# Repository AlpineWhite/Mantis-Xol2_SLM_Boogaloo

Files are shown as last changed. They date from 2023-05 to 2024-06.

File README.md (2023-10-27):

# SLMantis Xol 2 Aluminum Boogaloo (Slimfast)
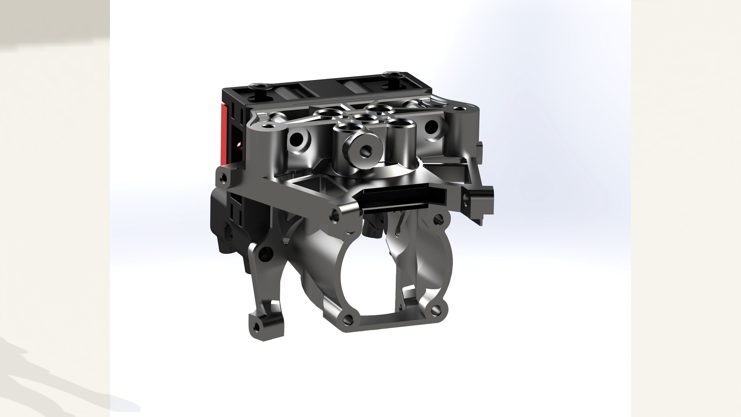
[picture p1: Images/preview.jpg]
Carriage Assembly The Metal Bits
   

## Description
Originally a project to slap 5020 blower fans onto Mantis, this toolhead variant started as an attempt to improve parts cooling, spurred on by Derpimus' noted cooling woes on his DOOMCube. After finding that the 5020s were just plain too fat to fit without looking like a standard Ender 3 Thingiverse special, I abandoned the large fan dream in favor of better cooling efficiency and lighter weight. This new and improved dream was also corrupted by my then budding and now all-consuming love for worm gears.

This was further pushed into the territory of abomination By deadwood83 who decided that plastic just wasn't metal enough, but a straight metal print was too heavy.  Since he was too plebian to have a worm-geared extruder, only Sherpa Mini support currently exists.

https://discord.gg/armchairengineeringsux

### Quick Links:
[Assembly / Tapping](https://github.com/AlpineWhite/Mantis-Xol2_SLM_Boogaloo/blob/main/Assembly.md)<br/>
[DragNet Bending Jig Usage](https://github.com/AlpineWhite/Mantis-Xol2_SLM_Boogaloo/tree/main/STL/Nets/DragNet/Bending%20Jig)<br/>
[RapidNet Bending Jig Usage](https://github.com/AlpineWhite/Mantis-Xol2_SLM_Boogaloo/tree/main/STL/Nets/RapidNet)<br/>
[RapidNet Grinding Jig Usage](https://github.com/AlpineWhite/Mantis-Xol2_SLM_Boogaloo/tree/main/STL/Nets/RapidNet/Grinding%20Jig) (For the Rapido Hotend)<br/>
[Probemounts](https://github.com/AlpineWhite/Mantis-Xol2_SLM_Boogaloo/tree/main/STL/XOL2%20SLiM%20V1.1%20%2B%20Probes/Probemounts)<br/>
[Breakout Toolhead PCB](https://github.com/AlpineWhite/Mantis-Xol2_SLM_Boogaloo/tree/main/SLiM%20PCB) <br/>
[My CNC Goals / How to Support Development](https://www.buymeacoffee.com/deadwood/first-post-first-steps)

## New Features for SLiMantis Xol 2
 - Cooler: Think Xol is ugly? This is not any better. But the entire hotend is now a heatsink.
 - Metaler: There is so much more metal. All inserts are replaced by tapped holes.
 - Rigid-er-er: Look at all that metal in the all-metal construction.
 - Supports Rapido, Dragon, Dragon UHF, Dragon+T-Volcano, Red Lizard all on one hotend mount.
 - Nets are created to attach the bottom of each hotend (except lizard) to the carriage. Nets are 304 stainless with 3d printed bending jigs. 

#### Features:
 - Better airflow than Stealthburner (6-7 CFM through short ducts vs 4.6-5.2 CFM through long ducts)
 - No inserts. No worries about thermal deformation.
 - Support for Sherpa Mini-pattern extruder mounting.
 - Symmetrical ziptie options.
 - Printed holes are already tap size.
 - Support for Whoppingpochard's Klicky PCB, OG Klicky, and bacon; but hardpoints on the bottom of the carriage allow for a modular approach to probing.
 - Top hardpoints allow development of custom tophats for your toolhead. Umbilical? Sure. Mantis tophat to bolt more stuff to your toolhead? Sure. Extruder apater plates which tie the carriage and hotend mount together? Sure.
 - Cross-compatibility with most of the XOL2 printed parts. You can combine metal hotend mount with a printed carriage, vice-versa, use printed ducts, printed faceplates, LED holder, nozzle camera mounts, etc. 
 - X axis microswitch in either direction (min/max/both except Kevin hates you for wanting to know your actual axis limits).
 
#### Future Development (No ETA):
 - MGN12 Carriage
 - Unnamed things because we have not discovered what else we may want to paste onto this.
 - Fancy ikon rail carriage support 

## Build Notes:
This toolhead might require other modifications to retain full functionality of your printer. 
 - All test machines used for this mod had Rama's front idlers which have a much lower profile compared to stock Voron front idlers. The fan assemblies might conflict and reduce usable X travel.
 - The Klicky Probe carriage that was adapted was originally designed for the Dragon hotend. You'll need to use a taller probe body to reach the bed such as the one used by [Unklicky BFP](https://github.com/majarspeed/Unklicky). *This isn't an issue for Euclid or PCB Klicky*.
## Bill of Materials 
|Item|Count|Note|
|----|-|--|
|Rapido|1|
|Sherpa Mini|1|CNC optional, but rigider-er-er|
|M2 Tap|1|[Use the tapered taps](https://www.amazon.com/gp/product/B07WGS6T3N) and WD-40 as lube|
|M2.5 Tap|1|
|M3 Tap|1|
|4010 24v blower fans|2|Add Polulu 3796 if you want the fancy 12v Deltas|
|2510 24v axial fan|1|
|M2x8 SHCS|6|
|M2x4 FHCS|2| Only for DragNet|
|M1.6 Low-Profile Nuts|2|Only for DragNet with T-Volcano|
|M2x12 SHCS|9|4 For Probe Mounts, 4 for fans, 1 for endstop|
|M2x6 SHCS|2|For Belt Pre-tension (optional)|
|M2.5x20 SHCS|4|For Cooling Fan|
|M2.5x8 90Deg FHCS|4|For Rapido mount|
|M3x8 BHCS|2|For Mount<->Carriage Lower Fasteners|
|M3x6 BHCS|1|For Sherpa K-mount|
|M3x10 90Deg FHCS|4|For carriage to rail mounting|
|M3x20-22 FHCS|4|Sherpa<->Hotend Mount and Hotend<->Carriage upper mount|
|D2F-5L Microswitch|1-2|
|M3x20-22 90Deg FHCS|2| For Hotend upper mounts on V1.1. 22mm gives 5mm of thread engagement. 20mm will work for both designs, just 22mm is slightly better for V1.1|
|ZIP TIES||

## Acknowledgement
[Long/Mandryd](https://github.com/mandryd/VoronUsers/tree/master/printer_mods/Long/Mantis_Dual_5015) for the Mantis toolhead.<br/>
[TheWarolf](https://github.com/TheWarolf/Voron-Personal-Mods/tree/main/V2/Long_Mantis_Toolhead) for the ERCF sensorized Hotend Mount.<br/>
[Derpimus](https://github.com/lraithel15133) for the exegesis, some CAD work, feedback, and just being a rad dude.<br/>
[KayosMaker](https://github.com/KayosMaker) for the MGN12 Klicky X-Carriage and CAN board mounts and spacers.<br/>
[JosAr](https://github.com/jlas1/Klicky-Probe) for Klicky.<br/>
[WhoppingPochard](https://github.com/tanaes) and [VinnyCordeiro](https://github.com/VinnyCordeiro/) for PCB Klicky.<br/>
[Nionio6915](https://github.com/nionio6915/Euclid_Probe) for Euclid. <br/>
[VoronDesign](https://github.com/VoronDesign) for this particular CoreXY flavor.<br/>
[AnnexEngineering](https://github.com/Annex-Engineering) for the Sherpa Mini and Double Folded Ascender extruders, and the K3 that influenced the air management of the ducts. And also for giving access to an early revision of the new DFA so it could be adapted for this toolhead.<br/>
[Clee](https://github.com/clee), you know what you did.  
[Takuya](https://github.com/T4KUUY4)... just added the 36mm SB2040 mount

Like my work? Want to support the cause?  I created a donation link because somebody asked how they can donate to me. [Here it is.](https://bmc.link/deadwood)

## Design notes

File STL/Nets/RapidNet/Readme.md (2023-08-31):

# RapidNet Bending Jig Usage
Print all parts at 100% infill.
All parts are in 'real' dimensions. You may need to scale 1% for shrinkage.
| Instruction | |
| --- | --- |
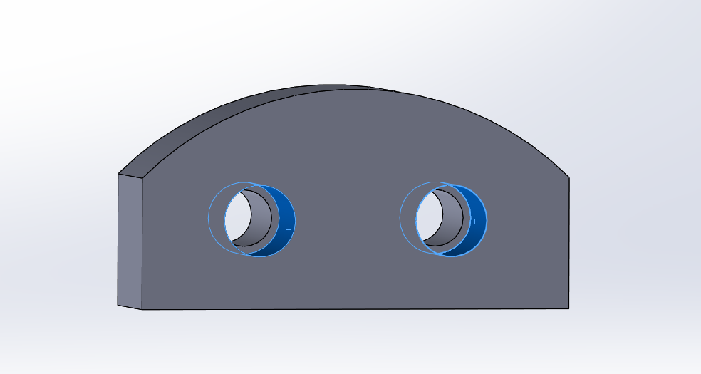
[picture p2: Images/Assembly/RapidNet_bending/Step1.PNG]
Clamp Heatsert Heatsert Installation
| Insert teo M3 heatserts into the clamping piece. This will interface with two M3x12SHCS.  |   |
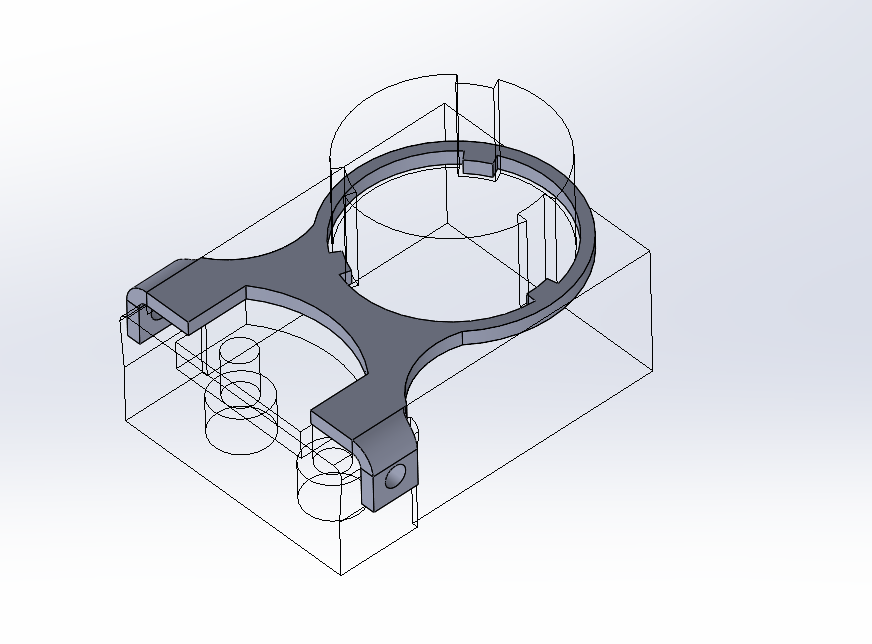
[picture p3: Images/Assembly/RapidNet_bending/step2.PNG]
Flat Positioning
| Lay the RapidNet flat into the bottom jig piece.  |    |
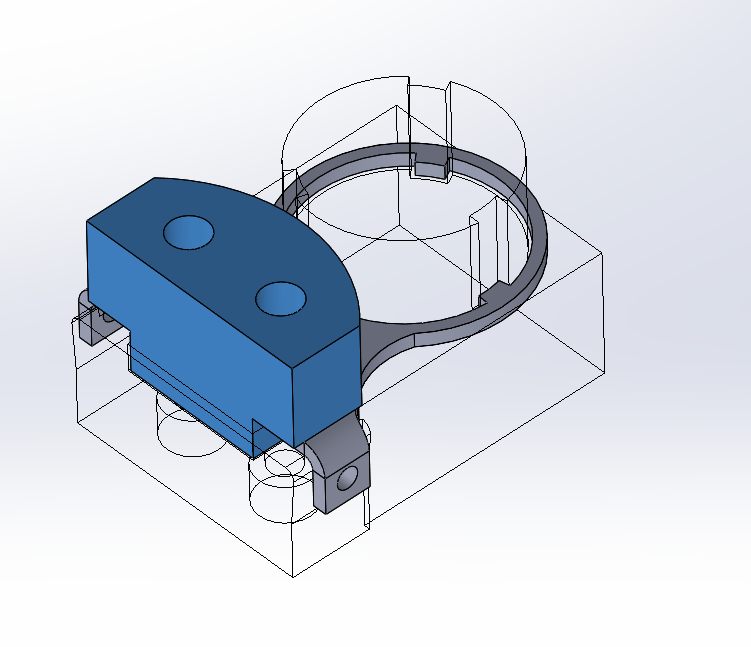
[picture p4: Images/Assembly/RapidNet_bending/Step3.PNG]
Clamping
| Insert the clamping piece into the recess, and fasten from the back with two M3 SHCS. |    |
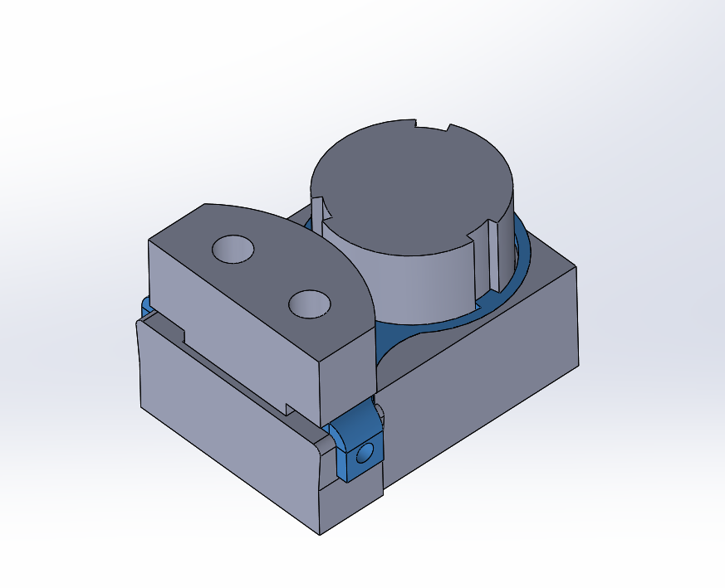
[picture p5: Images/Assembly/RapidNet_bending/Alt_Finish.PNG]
Hammertime Viseless Bending
| RECOMMENDED If you wish to use a hammer or other non-press/vise tool, press the tabs down against the plastic.  |   |
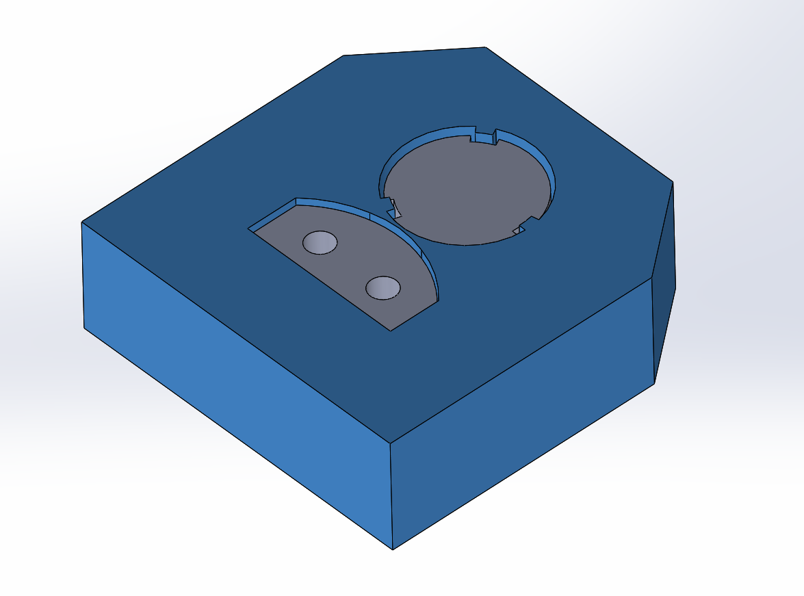
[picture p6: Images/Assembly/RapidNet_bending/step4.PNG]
Bending
| If using a vise or press, lay the top piece on the flat, and compress the sandwich to create the bend. |   |
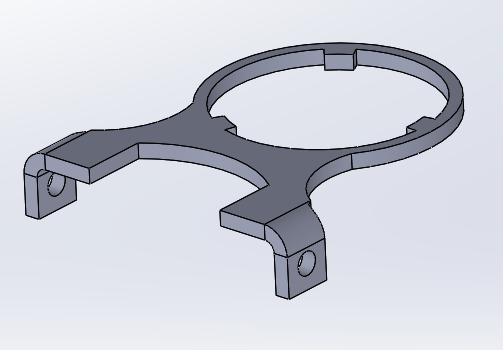
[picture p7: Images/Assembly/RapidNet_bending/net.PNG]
Finished Job Done
| Carefully remove the new-bent RapidNet from the jig. You may need to squeeze the tabs a little to compensate for springback. |   |

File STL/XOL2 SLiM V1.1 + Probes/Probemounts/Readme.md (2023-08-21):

For beacon:
 - There is a single part, but it must be mirrored to make each half of the mount. 
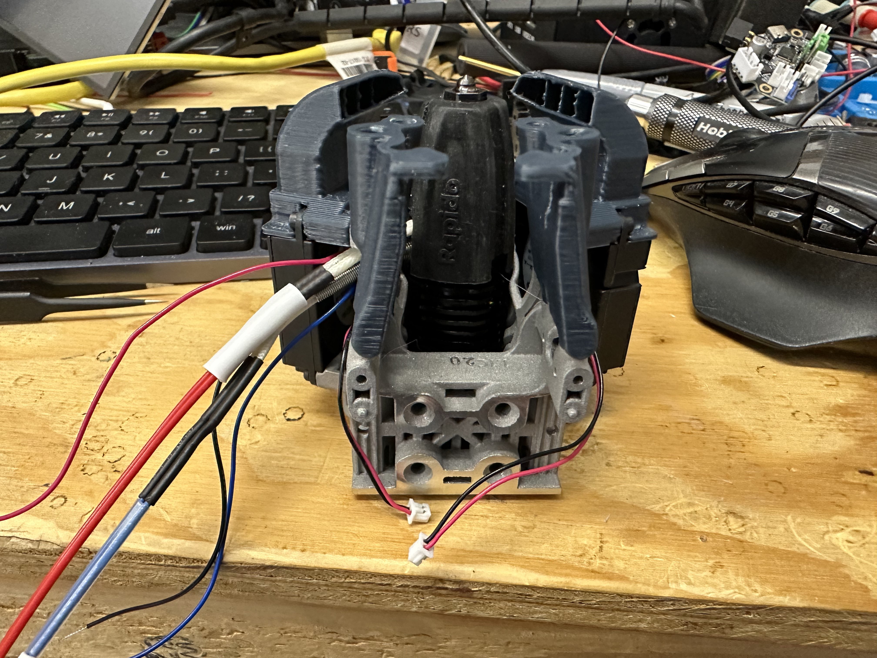
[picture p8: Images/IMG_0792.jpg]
Beacon Assembly Baconator


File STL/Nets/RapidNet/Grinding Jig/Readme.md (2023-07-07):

# RapidNet Grinding Jig Usage

| Instruction | |
| --- | --- |
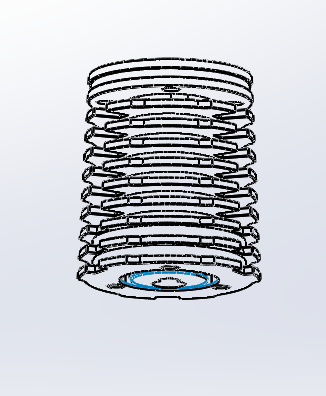
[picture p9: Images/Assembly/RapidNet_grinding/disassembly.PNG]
Disassemble Disassembly
| Remove the heater block from the Rapido and set aside. Keep the fasteners with the heater block. Only the heatsink is needed  |   |
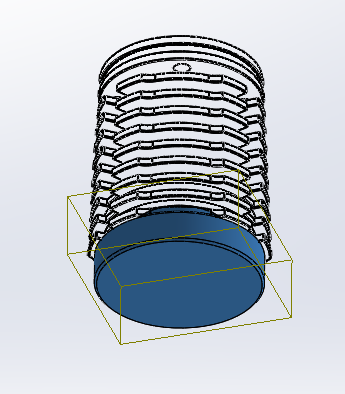
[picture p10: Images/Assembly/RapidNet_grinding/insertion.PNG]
Insertion Bow Chika Wow-wow
| Insert the printed part into the recess of the Rapido Heatsink.  |    |
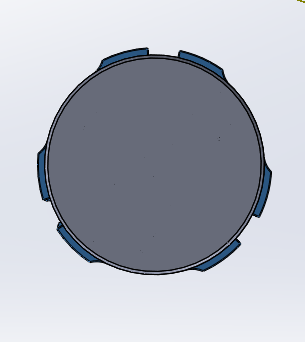
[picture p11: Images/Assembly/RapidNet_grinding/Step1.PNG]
Shaving Finless
| Remove the blue areas around the jig with a rotary tool or file. ONLY FILE/GRIND THE BOTTOM FIN. |    |
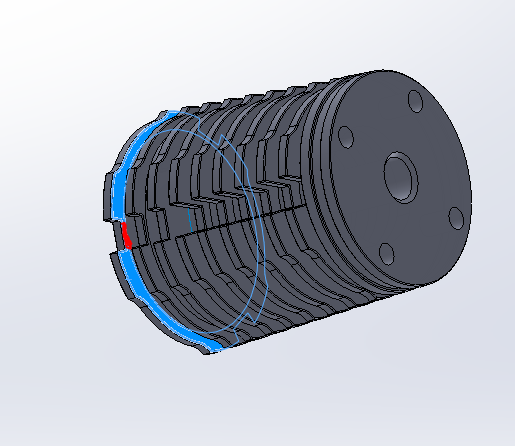
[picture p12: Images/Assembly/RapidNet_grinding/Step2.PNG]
Detail Work This may anger uncle arthur-itis.
| Remove the grinding jig, and use a rotary tool or file to grind/file the tiny lip marked in red down to flush with the inner circumference. Do this for all three relief cuts in the heatsink.  |   |
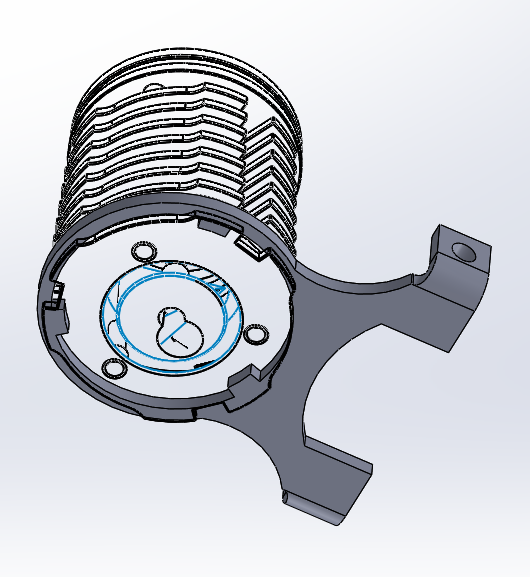
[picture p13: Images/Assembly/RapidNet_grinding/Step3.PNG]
You are done now Do the twist
| Slip the bent net onto Rapido by aligning the tabs with the three Rapido reliefs. Then twist a bit to secure. |   |

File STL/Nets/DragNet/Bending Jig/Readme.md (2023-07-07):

# DragNet Bending Jig Usage

| Instruction | |
| --- | --- |
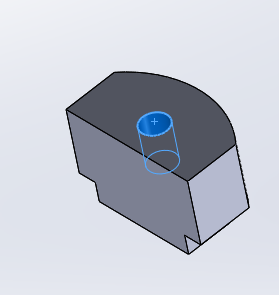
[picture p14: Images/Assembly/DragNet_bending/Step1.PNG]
Clamp Heatsert Heatsert Installation
| Insert an M3 heatsert into the clamping piece. This will interface with an M3x12FHCS.  |   |
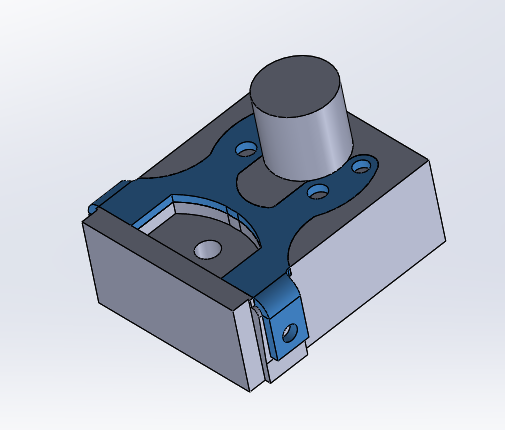
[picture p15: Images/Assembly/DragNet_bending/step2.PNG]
Flat Positioning
| Lay the DragNet flat into the bottom jig piece.  |    |
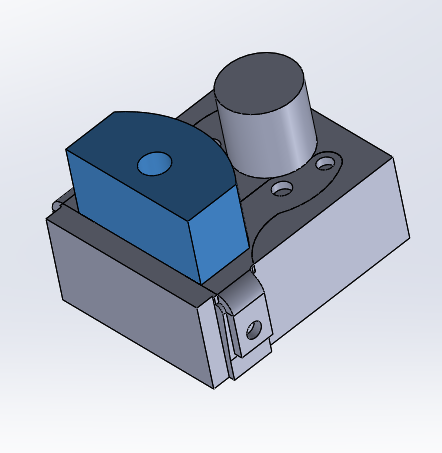
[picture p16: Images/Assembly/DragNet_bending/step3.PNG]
Clamping
| Insert the clamping piece into the recess, and fasten from the back with an M3 FHCS. |    |
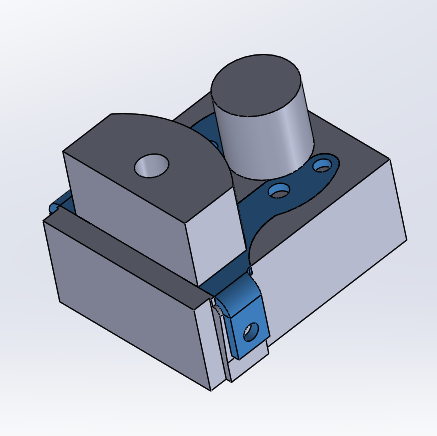
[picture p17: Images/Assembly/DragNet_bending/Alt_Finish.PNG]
Hammertime Viseless Bending
| If you wish to use a hammer or other non-press/vise tool, press the tabs down against the plastic.  |   |
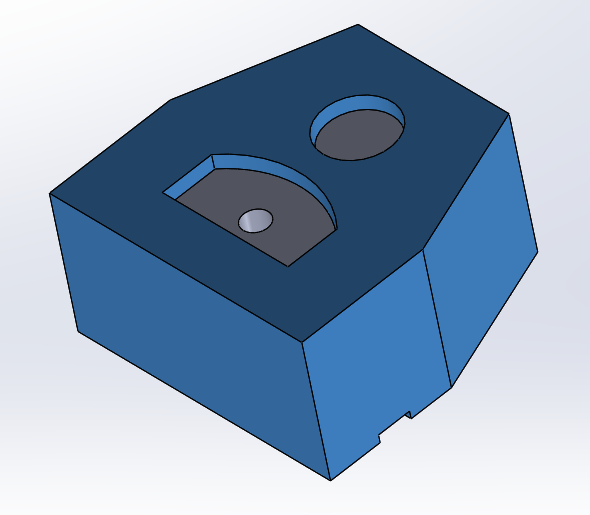
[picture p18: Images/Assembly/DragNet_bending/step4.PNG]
Bending
| If using a vise or press, lay the top piece on the flat, and compress the sandwich to create the bend. |   |
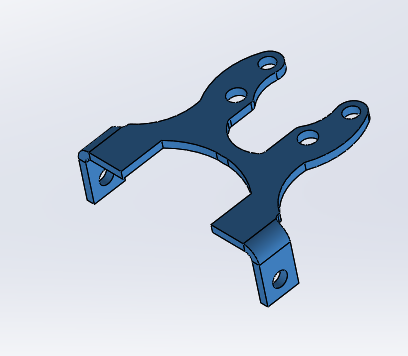
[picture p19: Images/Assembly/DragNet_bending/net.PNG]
Finished Job Done
| Carefully remove the new-bent DragNet from the jig. You may need to squeeze the tabs a little to compensate for springback. |   |

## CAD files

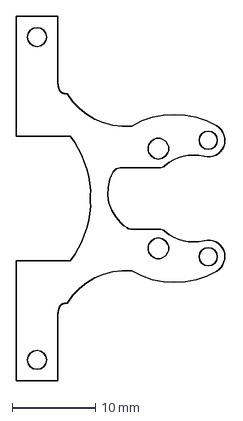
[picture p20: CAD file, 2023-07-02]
CAD/Xol2 SLiM/DragNet/Flat pattern - Dragnet.DXF
25.3 x 43.8 mm

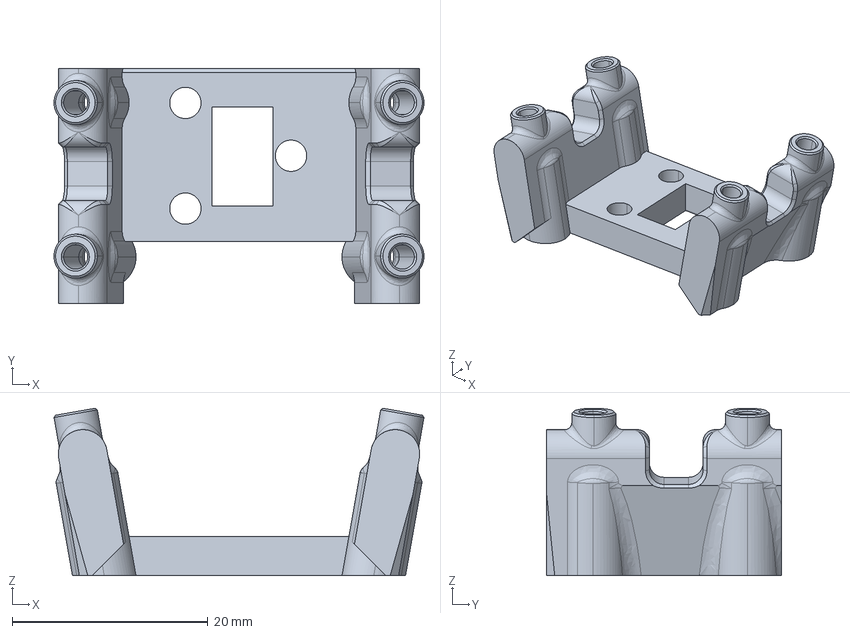
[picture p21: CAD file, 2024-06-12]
CAD/Xol2 SLiM/Probes/SLiM_-_PCB_Klicky_XolToolheadHeight_STD.stp
37.8 x 24.0 x 17.1 mm

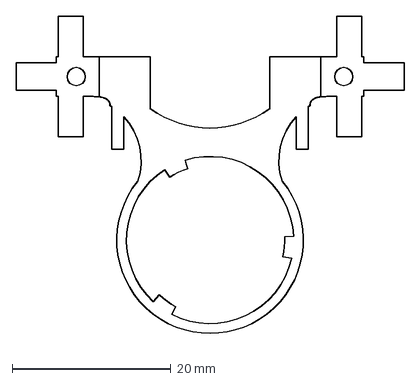
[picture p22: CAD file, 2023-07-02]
CAD/Xol2 SLiM/RapidNet/Flat For V1.1/Flat pattern - RapidNet^MultiBelt_Xol2_SLiM1.DXF
48.9 x 41.0 mm

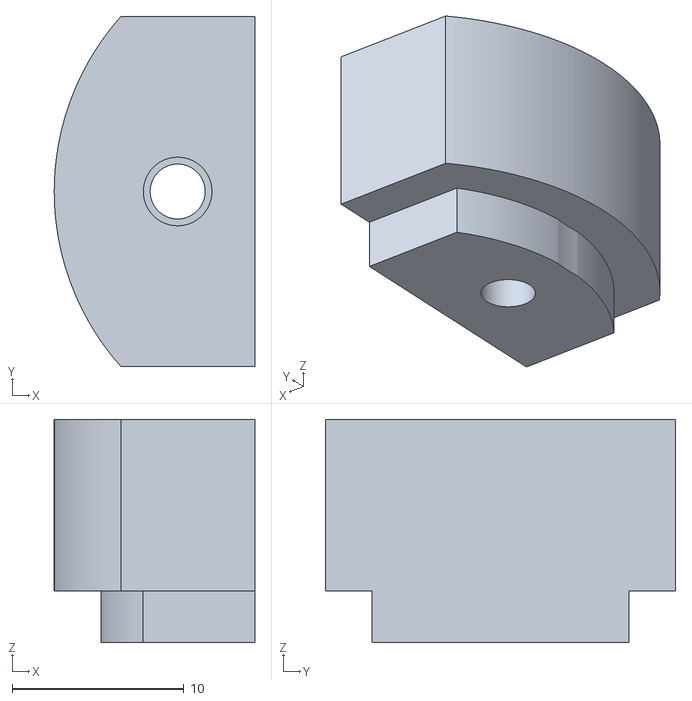
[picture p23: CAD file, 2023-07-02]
STL/Nets/DragNet/Bending Jig/Dragnet_Press_Jig_Clamp.STL
11.7 x 20.4 x 13.0

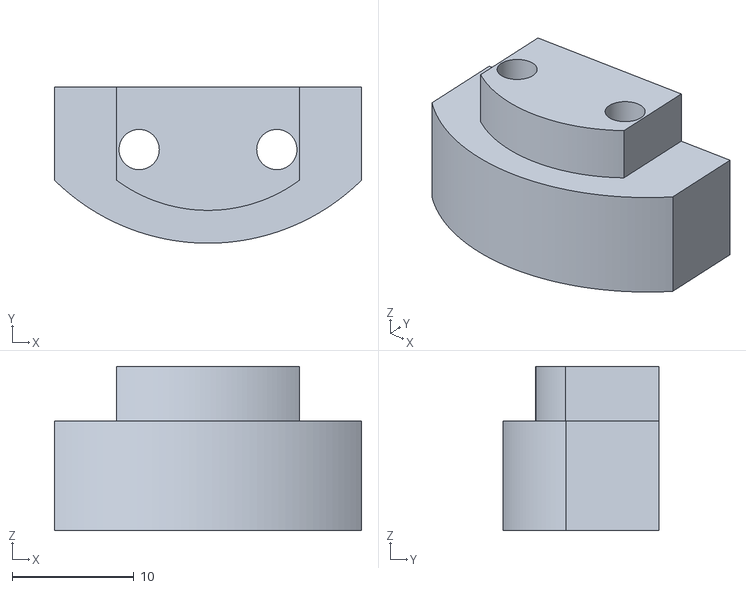
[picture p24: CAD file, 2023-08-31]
STL/Nets/RapidNet/Bending Jig/RapidNet_Locating_Peg.STL
25.2 x 12.8 x 13.5

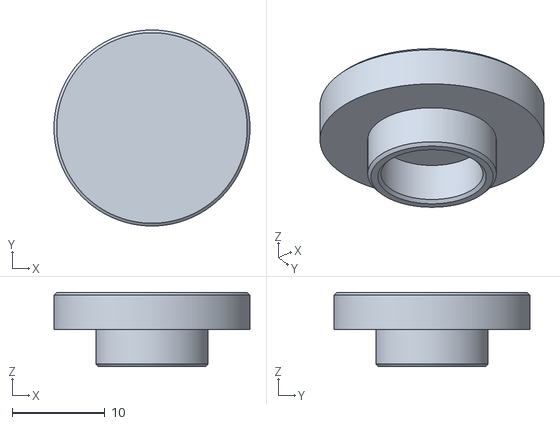
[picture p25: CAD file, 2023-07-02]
STL/Nets/RapidNet/Grinding Jig/RapidNet_Grinding_Jig.STL
21.1 x 21.1 x 8.00

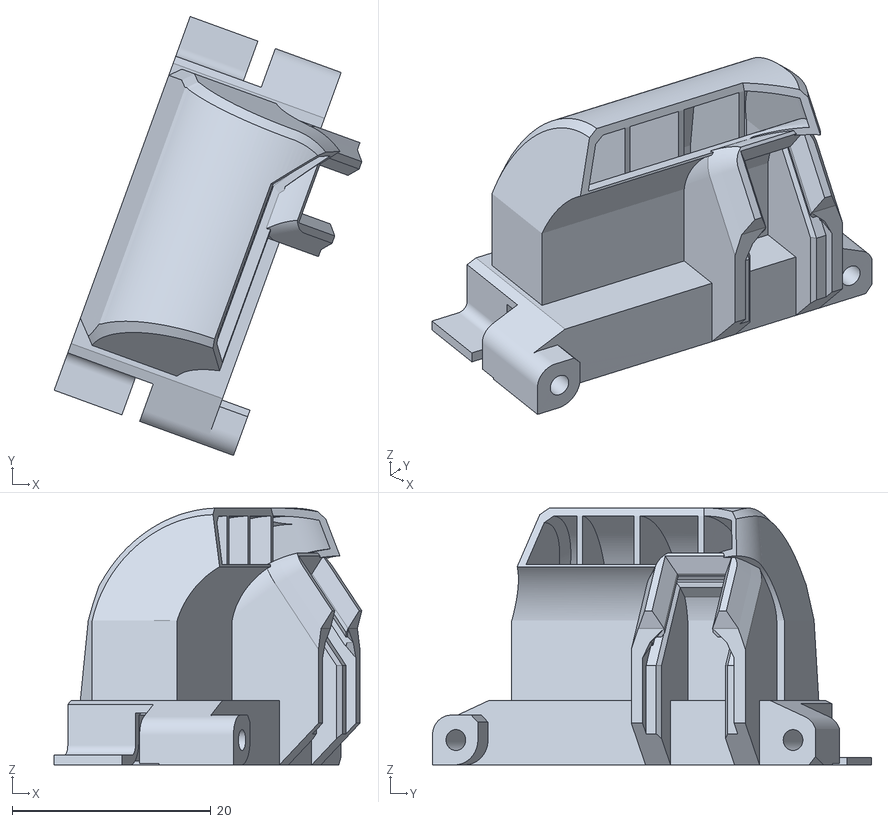
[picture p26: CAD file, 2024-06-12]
STL/Xol Toolhead (latest)/No-Tap/Ducts/Xol_LED_Ducts_UHF_-_Tri-Vane_Asym_Left_MOD3mm.STL
30.9 x 44.2 x 25.8

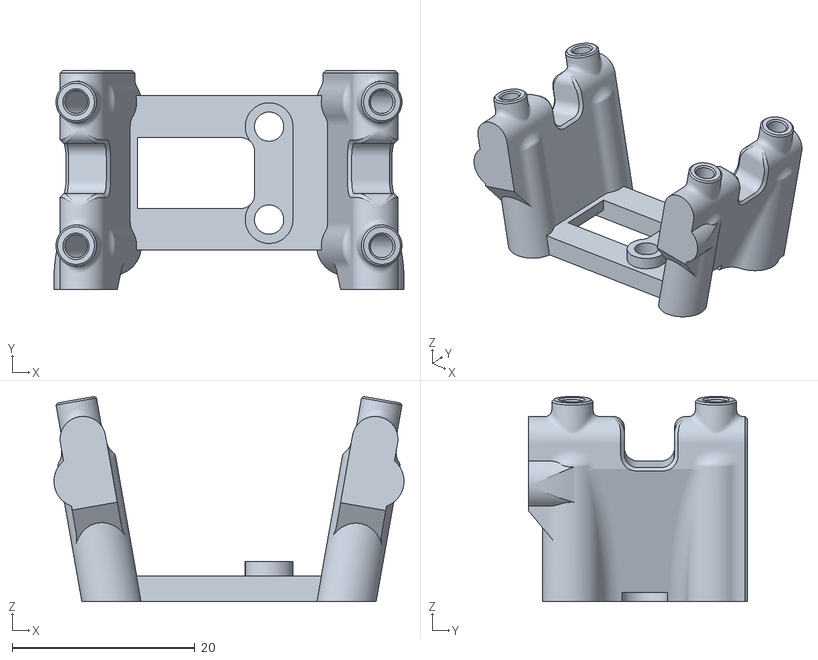
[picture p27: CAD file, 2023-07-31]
STL/XOL2 SLiM V1.1 + Probes/Probemounts/SLiM_-_Euclid_Carrier_UHF.stl
38.3 x 24.0 x 22.4

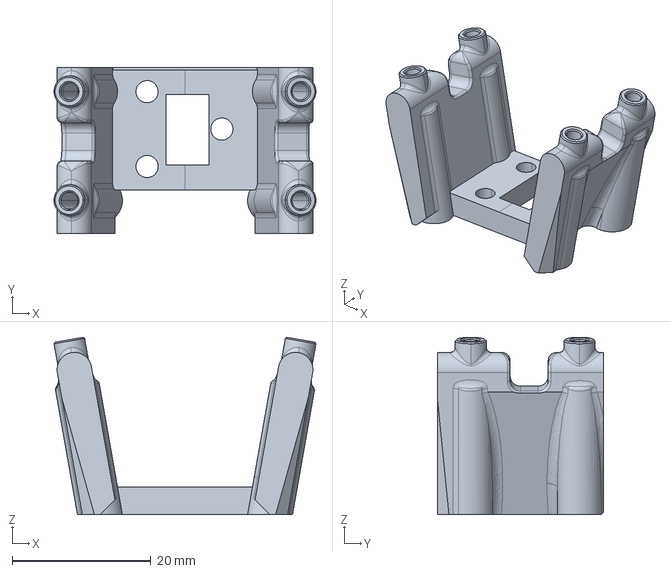
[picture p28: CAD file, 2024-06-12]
CAD/Xol2 SLiM/Probes/SLiM_-_PCB_Klicky_XolToolheadHeight_UHF.stp
37.8 x 24.0 x 25.6 mm

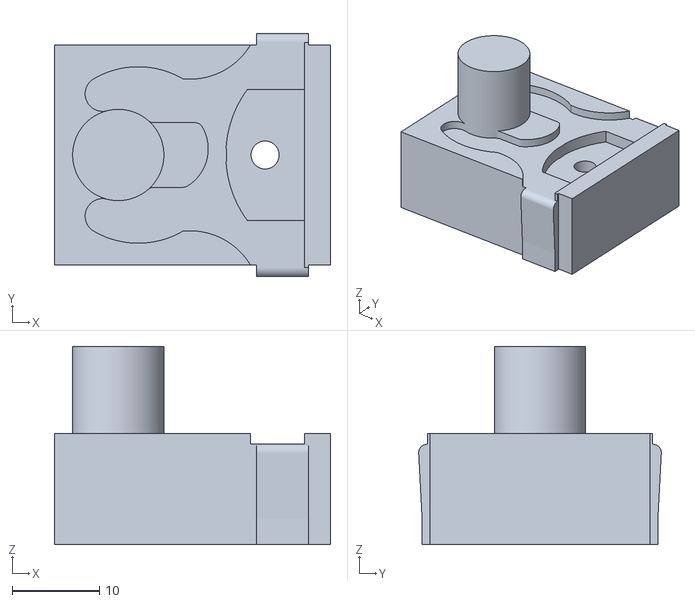
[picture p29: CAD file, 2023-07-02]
STL/Nets/DragNet/Bending Jig/Dragnet_Press_Jig_Base.STL
31.6 x 27.8 x 22.7

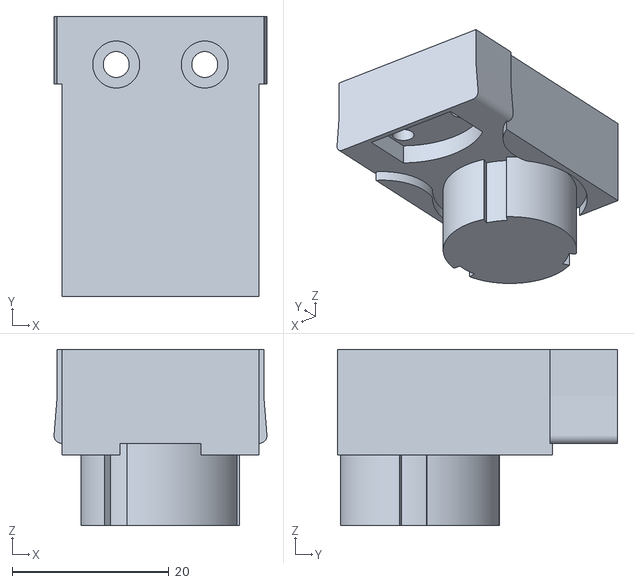
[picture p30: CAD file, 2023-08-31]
STL/Nets/RapidNet/Bending Jig/RapidNet_Bending_Base.STL
27.2 x 35.8 x 22.5

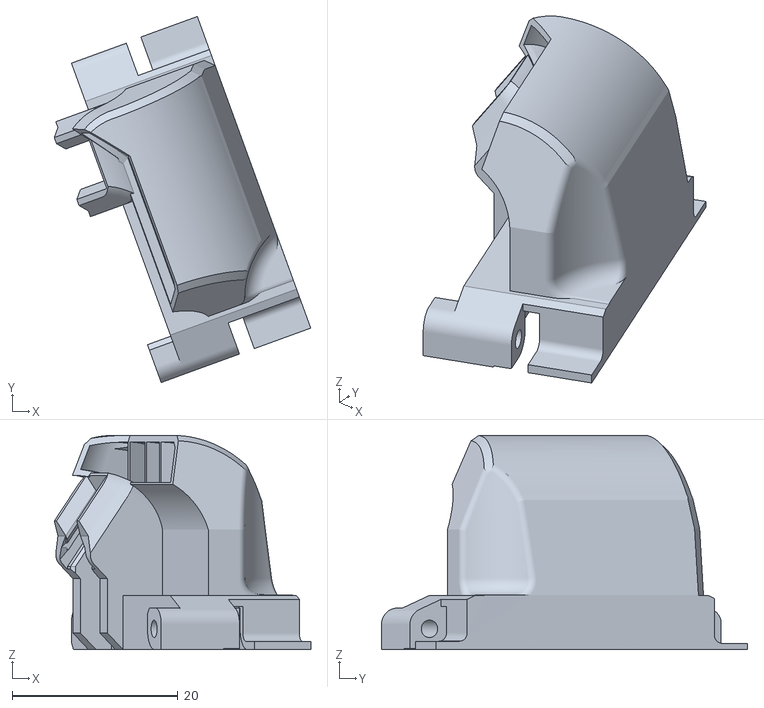
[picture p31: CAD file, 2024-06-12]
STL/Xol Toolhead (latest)/No-Tap/Ducts/Xol_LED_Ducts_UHF_-_Tri-Vane_Asym_Right_-_Trident_MOD3mm.STL
30.9 x 44.2 x 25.8

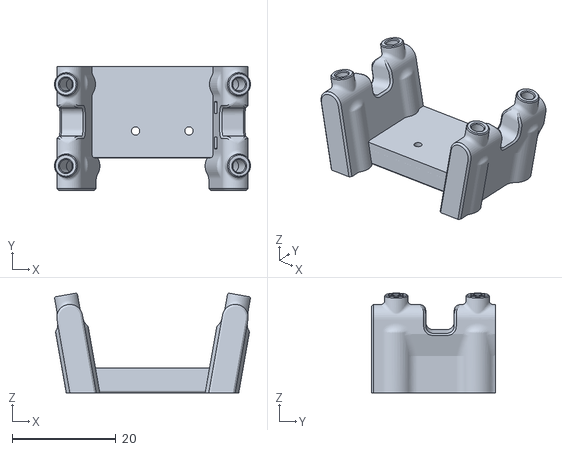
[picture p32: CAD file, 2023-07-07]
STL/XOL2 SLiM V1.1 + Probes/Probemounts/OG_Klicky_Beefy.STL
37.8 x 24.0 x 19.3

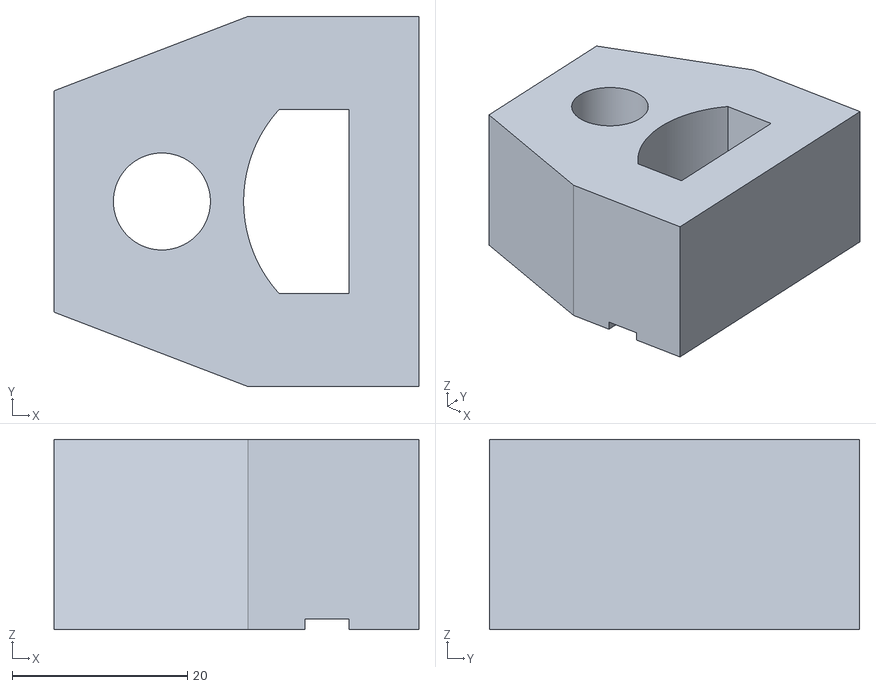
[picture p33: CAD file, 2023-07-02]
STL/Nets/DragNet/Bending Jig/Dragnet_Press_Jig_Top_Vise_Bending.STL
41.6 x 42.2 x 21.7

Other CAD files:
CAD/Xol2 SLiM/Probes/SLiM_-_Klicky_STD.STEP
STL/Nets/RapidNet/Bending Jig/RapidNet_Bending_Press.STL
STL/XOL2 SLiM V1.1 + Probes/Probemounts/OG_Klicky_Less_Beefy.STL
CAD/Xol2 SLiM/Probes/SLiM_-_PCB_Klicky_UHF.step
CAD/Xol2 SLiM/Probes/SLiM_-_Beacon_STD.step
CAD/Xol2 SLiM/Probes/SLiM_-_Euclid_UHF.step
CAD/Xol2 SLiM/Probes/SLiM_-_Klicky_Thicker_STD.STEP
CAD/Xol2 SLiM/Probes/SLiM_-_PCB_Klicky_STD.step
CAD/Xol2 SLiM/Probes/SLiM_-_PCB_Klicky_XolToolheadHeight_STD.stl
CAD/Xol2 SLiM/Probes/SLiM_-_PCB_Klicky_XolToolheadHeight_UHF.stl
CAD/Xol2 SLiM/RapidNet/Flat For V1/Flat pattern - Rapidnet_v1^MultiBelt_Xol2_SLiM.DXF

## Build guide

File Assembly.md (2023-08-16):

# Assembly of YOUR NEW SLMantis Xol 2 Toolhead

For printed parts other than [probemounts](https://github.com/AlpineWhite/Mantis-Xol2_SLM_Boogaloo/tree/main/STL/XOL2%20SLiM%20V1.1%20%2B%20Probes/Probemounts) and [nets](https://github.com/AlpineWhite/Mantis-Xol2_SLM_Boogaloo/tree/main/STL/Nets), please visit the archived [Armchair Enginnering Xol2 Repo](https://github.com/Armchair-Engineering/Mantis-Xol/tree/main/STL/Xol%202).

| Instruction | |
| --- | --- |
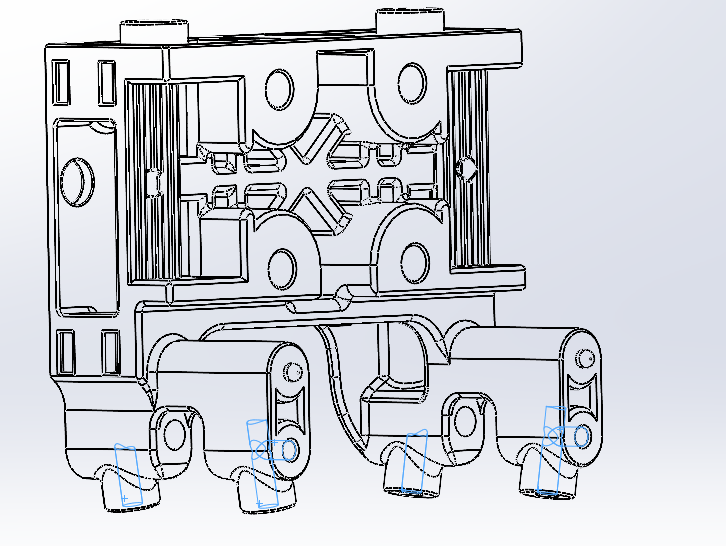
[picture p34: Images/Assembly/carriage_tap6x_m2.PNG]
Carriage M2 Holes Carriage M2 Tapped Holes
| Tap six M2 holes in the *Carriage* as indicated. The bottom four are for probe mounting and the rear two are for microswitches.  |   |
| Tap two M2 holes in the *Dogbone* as indicated for belt pretensioning.  |  Dogbone M2 Holes Belt Tensioning M2 Tapped Holes  |
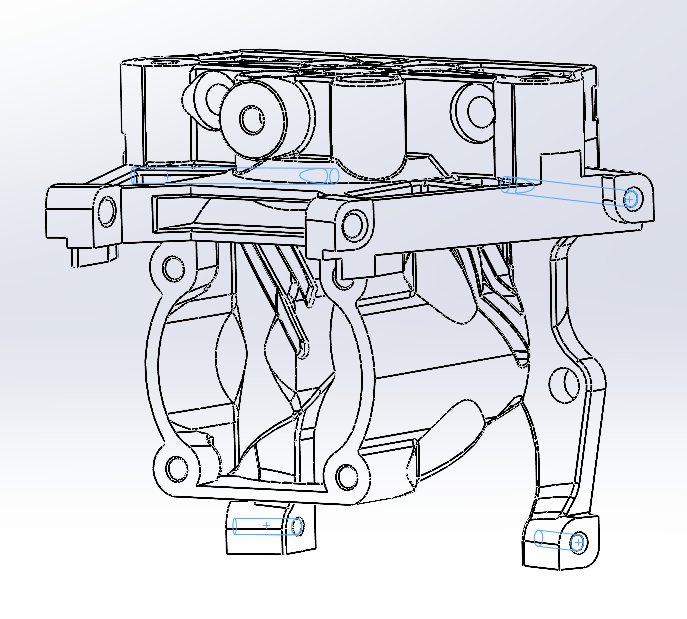
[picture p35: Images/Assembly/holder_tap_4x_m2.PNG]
Hotend Fan M2 Cooling Fan Tapped Holes
| Tap four M2 holes in the *Hotend Mount* for part cooling fans. You only need to go 8-10mm deep on the long rear holes. Going deeper risks breaking a tap. |    |
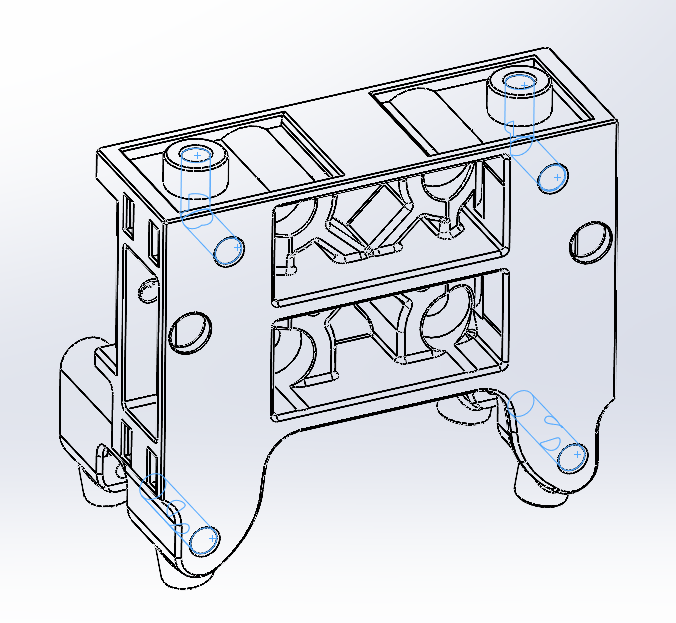
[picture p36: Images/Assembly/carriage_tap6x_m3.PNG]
Carriage M3 Holes Carriage M3 Tapped Holes
| Tap six M3 holes in the *Carriage* as indicated.  |   |
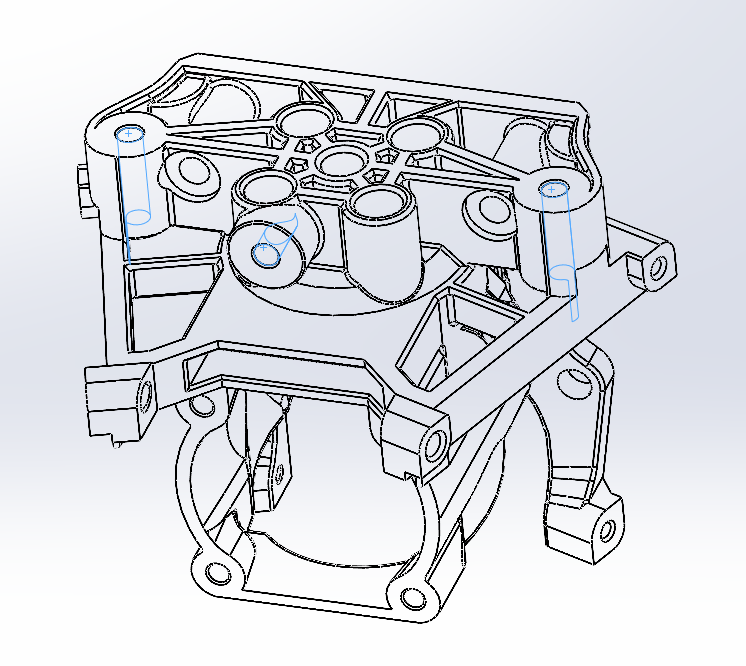
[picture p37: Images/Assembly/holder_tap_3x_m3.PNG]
Hotend Extruder Tapping Extruder M3 Threads
| Tap three M3 holes in the *Hotend Mount* for the extruder mounting. |   |
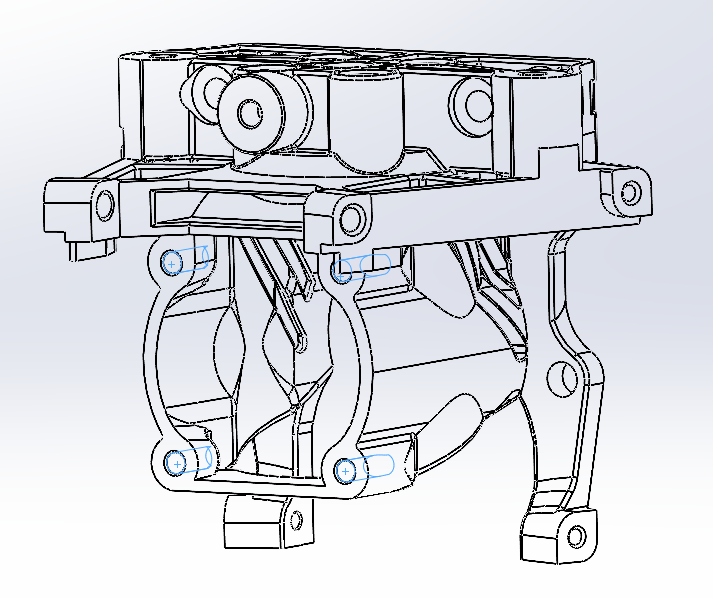
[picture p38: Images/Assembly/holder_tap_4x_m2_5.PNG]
Hotend Fan Tapping Hotend Fan Tapped Holes
| Finally, tap four M2.5 holes in the *Hotend Mount* as indicated for fan mounting. |   |
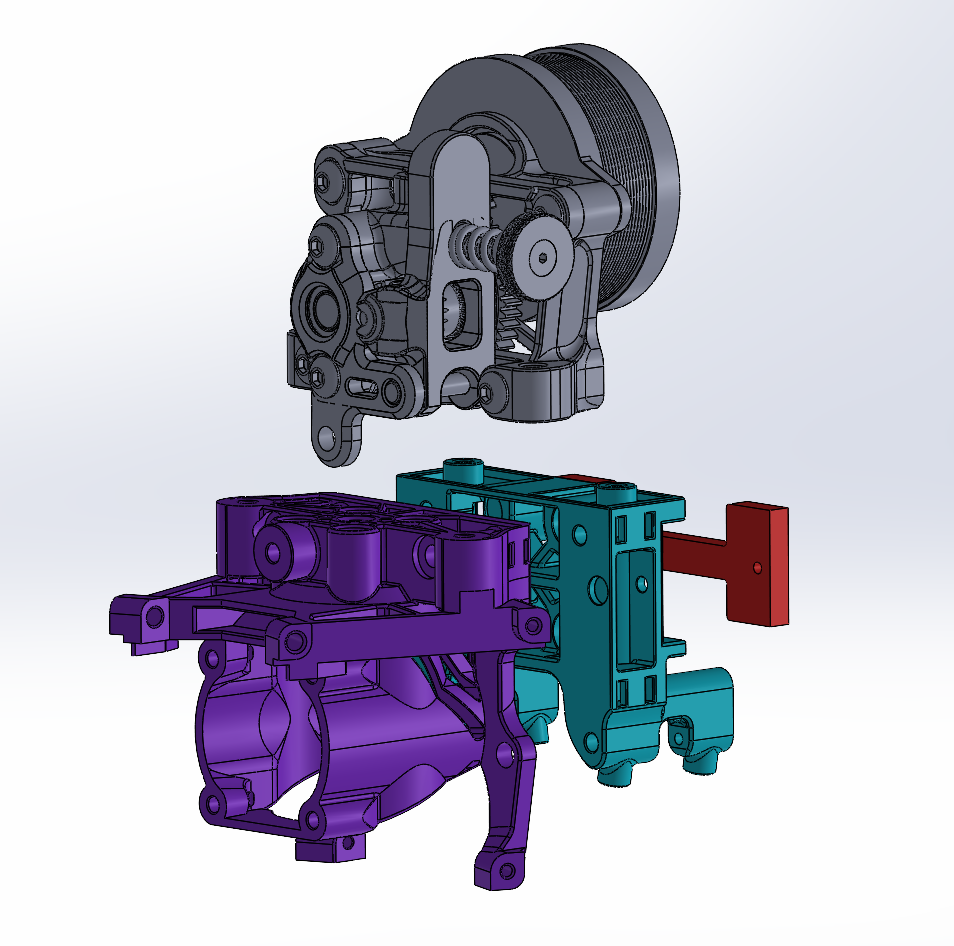
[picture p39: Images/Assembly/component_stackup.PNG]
Exploded View
| Ensure the dogbone solid surface is holding the belt smooth face. |   |

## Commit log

2023-06-28 Add V1.1 Initial CAD
2023-07-02 added nets and jigs
    Added bending jigs, grinding jig, net DXFs
    [Dragnet_Press_Jig_Base.STL, Dragnet_Press_Jig_Clamp.STL, Dragnet_Press_Jig_Top_Vise_Bending.STL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]
2023-07-07 RapidNet Grinding Jig Instructions
    [OG_Klicky_Beefy.STL, OG_Klicky_Less_Beefy.STL]
2023-07-31 Adding probes
    added cad for probes. added euclid courtesy of NyxCode
    [SLiM_-_Beacon_STD.step, SLiM_-_Euclid_Carrier_UHF.stl, SLiM_-_Euclid_UHF.step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]
2023-08-16 Update Assembly.md
    assembly links to nets, probemounts, and Xol2 STLs
2023-08-21 upload beacon mount attached image
    upload beacon mount attached image
2023-08-31 Update RapidNet Bending
    New bending fixtures for rapidnet
    [RapidNet_Bending_Base.STL, RapidNet_Bending_Press.STL, RapidNet_Locating_Peg.STL]
2023-10-27 Add SLiM PCB
2023-10-27 SLIM PCB Gerbers
2023-12-04 Xoltoolhead height pcb_klicky probe mounts
    These mounts are 5mm taller than SLM pcb_klicky mounts. Allow use of the Klicky-00 probe with PCB klicky. Rapido (STD) and UHF mounts were modified.
    [SLiM_-_PCB_Klicky_XolToolheadHeight_STD.stl, SLiM_-_PCB_Klicky_XolToolheadHeight_STD.stp, SLiM_-_PCB_Klicky_XolToolheadHeight_UHF.stl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]
2024-06-11 UHF ducts compatible with New Xol Toolhead faceplates
    [Xol_LED_Ducts_UHF_-_Tri-Vane_Asym_Left_MOD3mm.STL, Xol_LED_Ducts_UHF_-_Tri-Vane_Asym_Right_-_Trident_MOD3mm.STL]
